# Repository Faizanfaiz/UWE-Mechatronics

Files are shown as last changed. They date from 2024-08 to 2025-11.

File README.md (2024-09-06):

# Single-Leg Robot Dog Project

This repository contains the setup, code, and documentation for the development of a single-leg robot dog. The project is designed to provide a platform for students to experiment with robotic leg control, dynamics, and various motor control algorithms using a Raspberry Pi 5 and RMD X motors.

## Table of Contents
- [Project Overview](#project-overview)
- [Hardware Requirements](#hardware-requirements)
- [Software Setup](#software-setup)
- [License](#license)

## Project Overview
The objective of this project is to develop a single robotic leg that can be used as a testbed for students learning about robotic control systems, motor dynamics, and gait patterns. The robotic leg is powered by RMD X motors and controlled via a Raspberry Pi 5, interfaced through a Waveshare 2-Channel CAN FD HAT. This platform allows for practical experimentation in a controlled environment.

## Hardware Requirements
For the full list of hardware and BOM click [here](https://github.com/Faizanfaiz/UWE-Mechatronics/tree/main/Parts#hardware)
- Raspberry Pi 5
- Waveshare 2-Channel CAN HAT
- RMD-X8 Motors
- Power Supply for Raspberry Pi and Motors
- MicroSD Card (with Raspberry Pi OS 64-bit installed)
- Mechanical components for the robotic leg (joints, frame, etc.)
- CAN Bus cables and connectors

## Software Setup
### 1. Install Raspberry Pi OS (64-bit)
Ensure your Raspberry Pi is running the 64-bit version of Raspberry Pi OS.

### 2. Setup Waveshare 2-CH CAN HAT/ 2-CH CAN FD HAT
Before Following any of the instructions below, make sure you check your expnasion Board and Follow the relevant Instructions:

Follow the instructions provided by Waveshare to set up the 2-Channel CAN HAT. The detailed guide can be found here: [Waveshare 2-CH CAN HAT Setup Guide](https://www.waveshare.com/wiki/2-CH_CAN_HAT).

Follow the instructions provided by Waveshare to set up the 2-Channel CAN FD HAT. The detailed guide can be found here: [Waveshare 2-CH CAN FD HAT Setup Guide](https://www.waveshare.com/wiki/2-CH_CAN_FD_HAT).

### 3. Install Required Dependencies
Install the necessary software packages and dependencies for motor control and CAN communication:
\`\`\`bash
sudo apt-get update
sudo apt-get install can-utils python-can
\`\`\`

### 4. Configure the CAN Interface
Configure the CAN interface to communicate with the RMD X motors. Follow the Waveshare guide for initial setup, and then set the bitrate and interface settings as needed:
\`\`\`bash
sudo ip link set can0 up type can bitrate 1000000
\`\`\`

## License
This project is licensed under a proprietary license for exclusive use by [University Name]. Unauthorized use outside the university is prohibited.

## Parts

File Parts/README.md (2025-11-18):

[pointers to item links below]: #

[RMD-x8]: https://uk.robotshop.com/products/my-actuator-rmd-x8-pro-v2-can-bus-bldc-actuator-w-19-reduction-mc-x-300-o-driver
[PI]: https://thepihut.com/products/raspberry-pi-5?variant=42531604955331
[SD]: https://uk.rs-online.com/web/p/sd-cards/2836581
[CAN-HAT]: https://www.waveshare.com/2-ch-can-fd-hat.htm

[M4I]: https://ebay.us/m/BUPcYn
[M4x30C]: https://ebay.us/m/XLIqXn
[M4x20C]: https://ebay.us/m/y3svrC
[M4x16C]: https://ebay.us/m/ICN1YX
[M4x8C]: https://ebay.us/m/ASdklv
[M4x10CS]: https://ebay.us/m/useJ9E
[M5x35BH]: https://ebay.us/m/N0DYHb
[M5N]: https://ebay.us/m/qY9aDb
[M4N]: https://ebay.us/m/3rJfDg
[TP26]: https://www.bearingboys.co.uk/5M-Section-Timing-Pulley-5mm/265M15-Metric-Pilot-Bore-Timing-Pulley-21236-p
[TB635]: https://www.bearingboys.co.uk/5M-Section-5mm-Pitch/6355M15-Timing-Belt-6109-p
[B22]: https://www.bearingboys.co.uk/Miniature-Bearings/6082RS-Dunlop-Sealed-Miniature-Steel-Ball-Bearing-8mm-x-22mm-x-7mm-7728-p
[B12]: https://www.bearingboys.co.uk/Miniature-Bearings/MR128ZZ-Budget-Shielded-Miniature-Ball-Bearing-8mm-x-12mm-x-35mm--140413-p

[EX2020]: https://ooznest.co.uk/product/20x20mm-t-v-slot-aluminium-extrusion-profile-silver-cut-to-size/
[SBR12]: https://ebay.us/m/hoO5Eb

# Parts list
This document shows everything needed to build the leg, for the assembly please read the [Assembly Guide](https://github.com/Faizanfaiz/UWE-Mechatronics/tree/main/Assembly#assembly). 

## 3D prints
>[!NOTE]
>All parts can fit on a minimum printer bed size of 256x256mm.  
>Everything was printed on the Bambu Lab A1 and X1 Carbon in PolyTerra PLA Fossil Grey.

### Print settings
- 35% infill
- Triangular infill
- Supports enabled
- 2 or 3 layer thick walls
- Bottom Z distance = 0.08mm
- Outer and inner brim 5mm

### 
| Thumbnail | Name | Quantity |
|:---:|:---:|:---:|
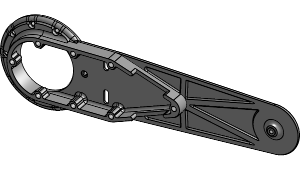
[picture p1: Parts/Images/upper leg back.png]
|  | upper leg back | 1 |
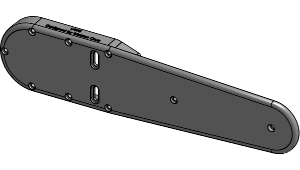
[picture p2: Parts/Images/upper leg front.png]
|   | upper leg front | 1 |
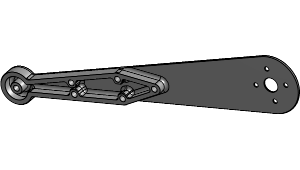
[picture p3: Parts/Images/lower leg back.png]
|  | lower leg back | 1 |
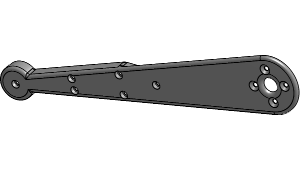
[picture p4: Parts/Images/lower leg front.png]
|   | lower leg front | 1 |
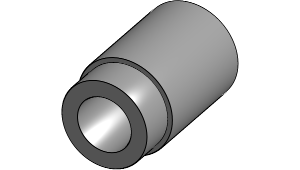
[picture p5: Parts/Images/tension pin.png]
|  | tension pin | 4 |
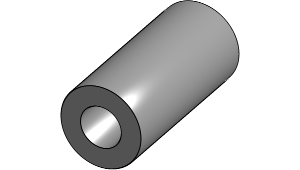
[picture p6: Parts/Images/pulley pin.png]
|  | pulley pin | 1 |
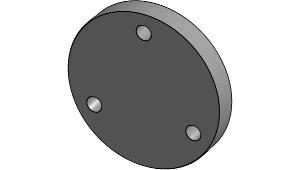
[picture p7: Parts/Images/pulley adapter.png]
|  | pulley adapter | 1 |
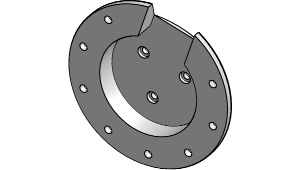
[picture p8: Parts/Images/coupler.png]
|  | coupler | 1 |
|  | motor plate | 1 |

### Depreciated
| Thumbnail | Name | Reason |
|:---:|:---:|:---:|
| | | |

## Hardware
### Electronics needed
>[!NOTE]
>The motor can be swapped for similar motors with same diameter and bolting layout.

| Item + Link | Short description | Quantity | Cost per item |
|---|---|:---:|:---|
| [RMD-X8 motor][RMD-x8] | drive the upper and lower leg | 2 | ~£400 |
| [Raspberry pi 5 8GB][PI] | main board for executing code | 1 | £76.80 |
| [waveshare 2CH CAN FD HAT][CAN-HAT] | SPI to CAN conversion | 1 | £35.75 |
| [SD card 32GB][SD] | raspeberry pi os 64x installed | 1 | £9.98 |
| **Total** | | | **£1,322.53** |

### Hardware for the leg
| Item + Link | Short description | Quantity | Cost per item/pack |
|:---|:---|:---:|:---|
| [M4 inserts][M4I] | one side of both upper and lower leg | 14 | £6.49 / 50 pack |
| [M4x30 cap][M4x30C] | pulley pin | 1 | £3.42 / 5 pack |
| [M4x20 cap][M4x20C] | upper leg enclosure | 8 | £3.84 / 10 pack |
| [M4x16 cap][M4x16C] | lower leg enclosure | 6 | £3.54 / 10 pack |
| [M4x8 cap][M4x8C] | coupler between both motors and the leg | 11 | £4.00 / 20 pack |
| [M4x10 countersunk][M4x10CS] | attaching driven pulley to lower leg | 8 | £3.03 / 10 pack |
| [M5x35 button head][M5x35BH] | pulley tensioner | 2 | £3.54 / 5 pack |
| [M5 nut][M5N] | pulley tensioner | 2 | £2.64 / 5 pack |
| [M4 nut][M4N] | pulley pin | 1 | £2.64 / 5 pack |
| [26-5M-15 Timing Pulley][TP26] | moving the lower leg | 2 | £8.20 |
| [635-5M-15 Timing Belt][TB635] | moving the lower leg | 1 | £7.37 |
| [22x8x7mm bearing][B22] | for the pulleys | 3 | £2.04 |
| [12x8x3.5mm bearing][B12] | for the belt tensioner | 4 | £2.61 |
| **Total** | | | **£67.76** |

### Hardware for the frame
| Item + Link | notes | Quantity | cost per item  |
|:---|:---|:---:|:---|
| [2020 extrusion 1.2m][EX2020] | cut/ordered to length  | 3 | £9.22 |
| [SBR12 linear guide rail 500mm 2pcs][SBR12] | | 2 | £26.59 |
| **Total** | | | **£80.84** |

### Total cost: ~£1,471.13 (Subject to change)

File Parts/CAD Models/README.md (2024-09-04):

This folder contains all the 3D models for the robot leg.

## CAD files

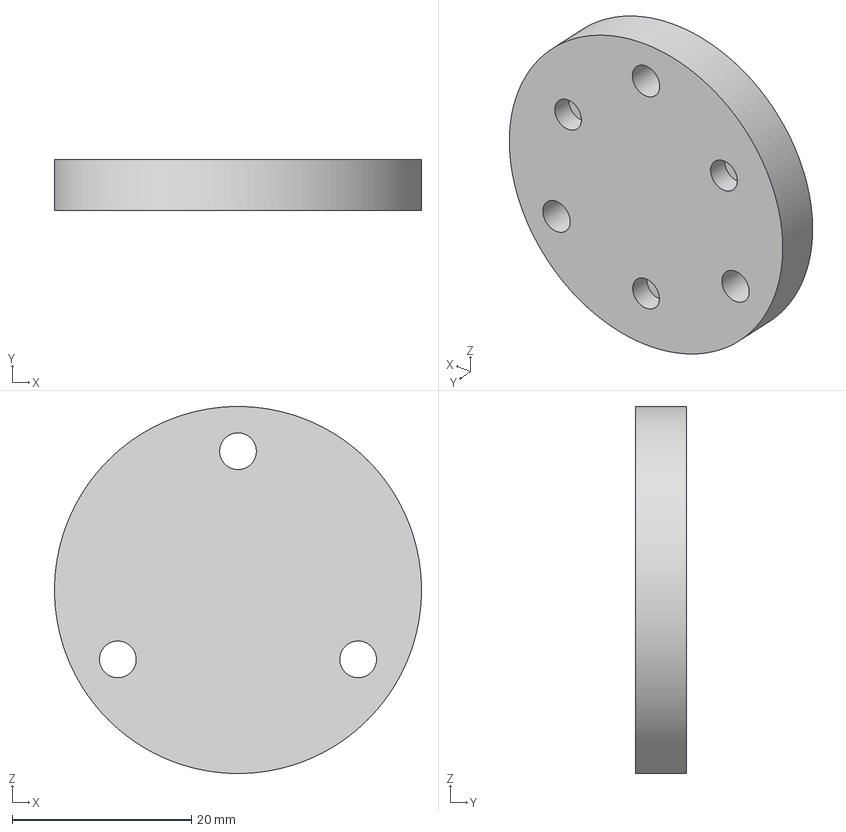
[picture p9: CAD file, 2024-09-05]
Parts/CAD Models/driver pulley adapter.3mf
41.0 x 5.75 x 41.0 mm

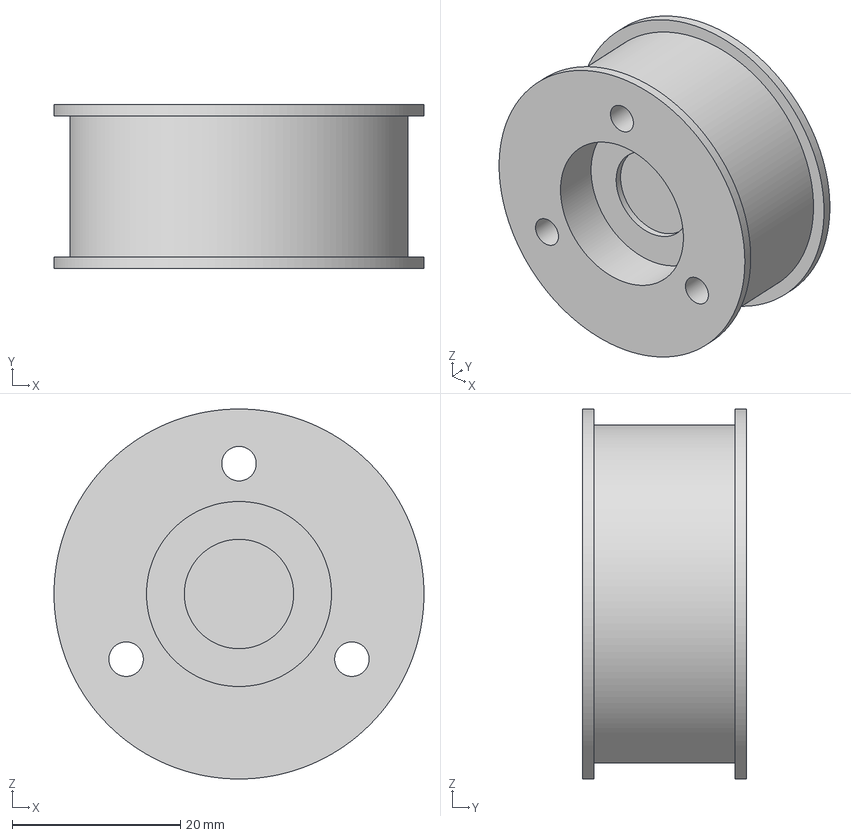
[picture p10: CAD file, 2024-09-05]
Parts/CAD Models/driver pulley.3mf
44.0 x 19.5 x 44.0 mm

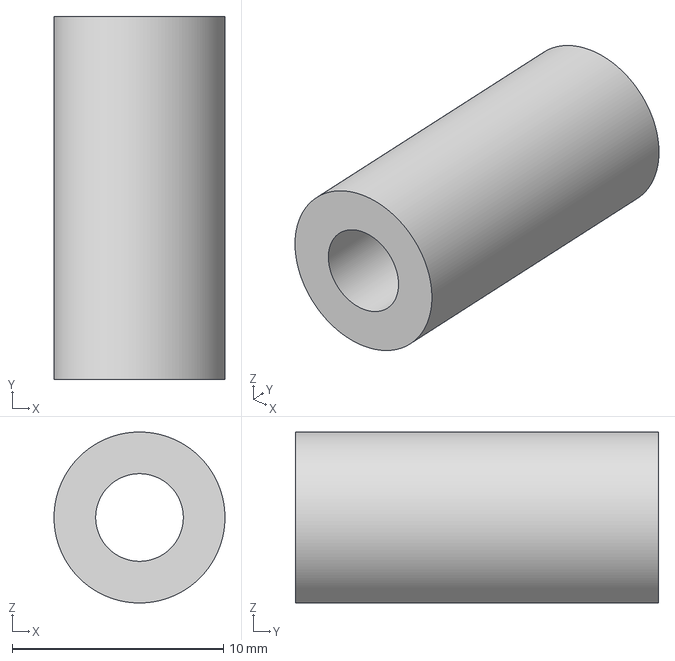
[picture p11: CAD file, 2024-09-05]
Parts/CAD Models/bearing pin.3mf
8.10 x 17.2 x 8.10 mm

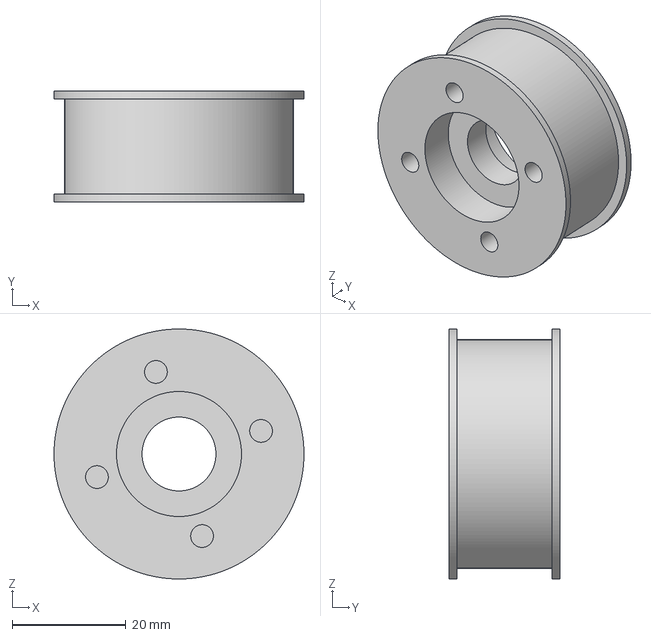
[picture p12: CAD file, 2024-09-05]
Parts/CAD Models/driven pulley.3mf
44.0 x 19.5 x 44.0 mm

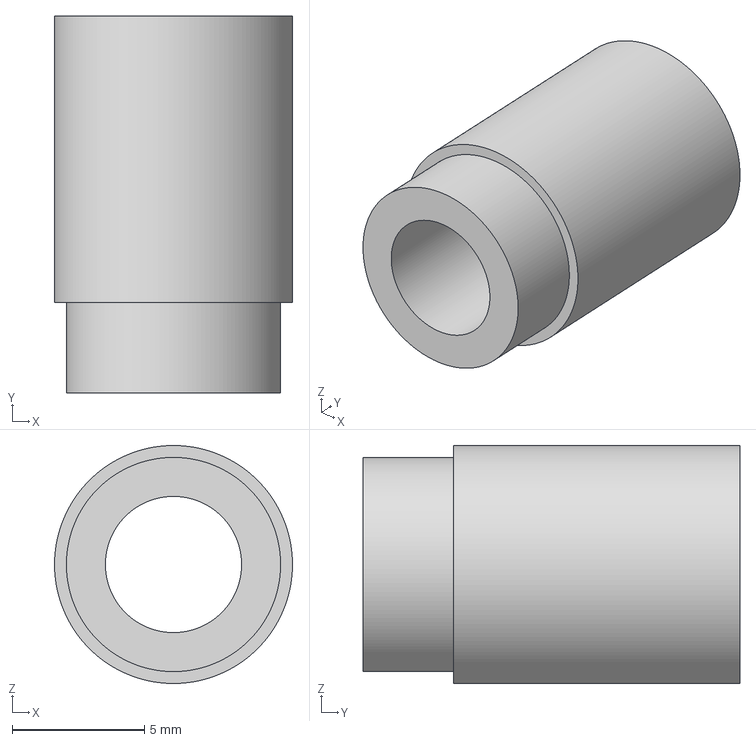
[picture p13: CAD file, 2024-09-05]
Parts/CAD Models/tension pin.3mf
9.00 x 14.2 x 9.00 mm

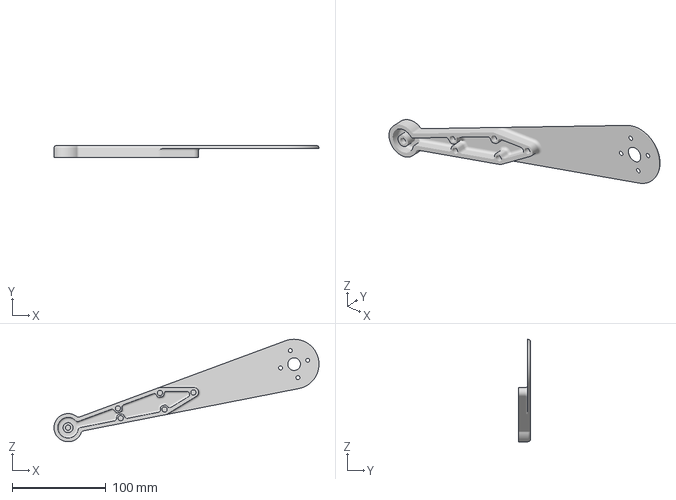
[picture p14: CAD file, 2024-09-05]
Parts/CAD Models/lower leg.3mf
282.2 x 12.8 x 109.1 mm

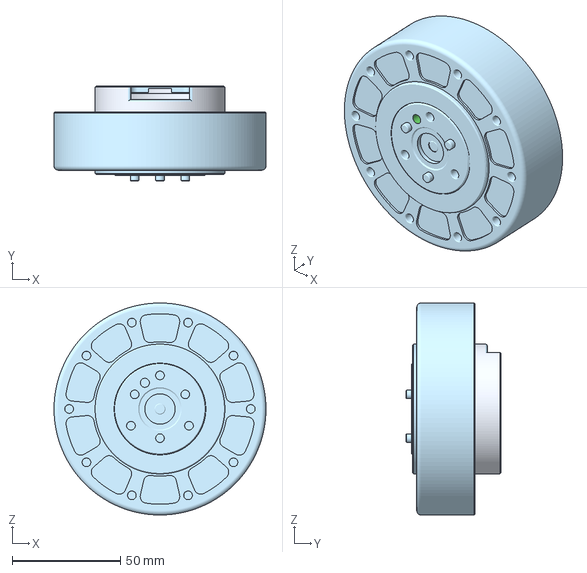
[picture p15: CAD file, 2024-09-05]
Parts/CAD Models/RMD-X8.3mf
98.0 x 44.0 x 98.0 mm

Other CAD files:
Parts/CAD Models/lower leg cover.3mf

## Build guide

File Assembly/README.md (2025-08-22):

# Assembly
This document shows the assembly process for the [robot leg](#robot-leg) and [frame](#frame). Ensure that you have all the [hardware](https://github.com/Faizanfaiz/UWE-Mechatronics/blob/main/Parts/README.md#hardware) and [3D-prints](https://github.com/Faizanfaiz/UWE-Mechatronics/blob/main/Parts/README.md#3d-prints) from the [Parts](https://github.com/Faizanfaiz/UWE-Mechatronics/tree/main/Parts#parts-list) list.

>[!NOTE]
>Previously assembled components may be excluded from some images to simplify the viewing of each step. Compare your build to the checks along the way.

# Robot leg
>[!IMPORTANT]
>Before starting the leg assembly, heat press the M4 threaded inserts into the holes labeled below. [Here](https://youtu.be/P7nHyI1TwKY?t=188&si=k5AsJouK1HimsCW4) is a video explaining how to do this.

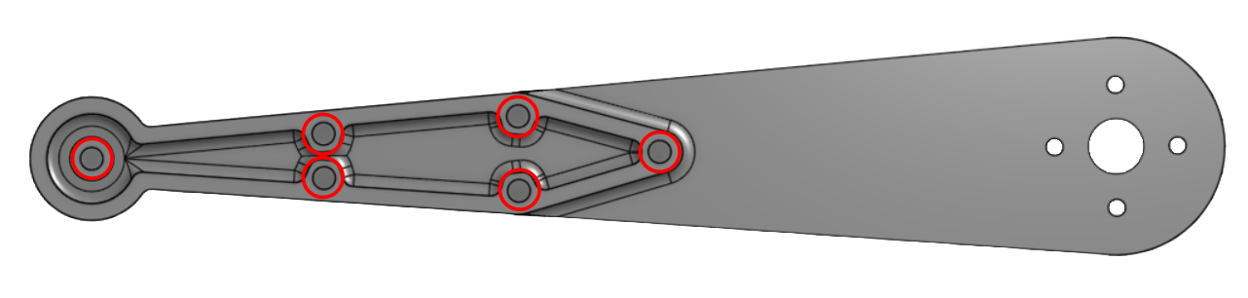
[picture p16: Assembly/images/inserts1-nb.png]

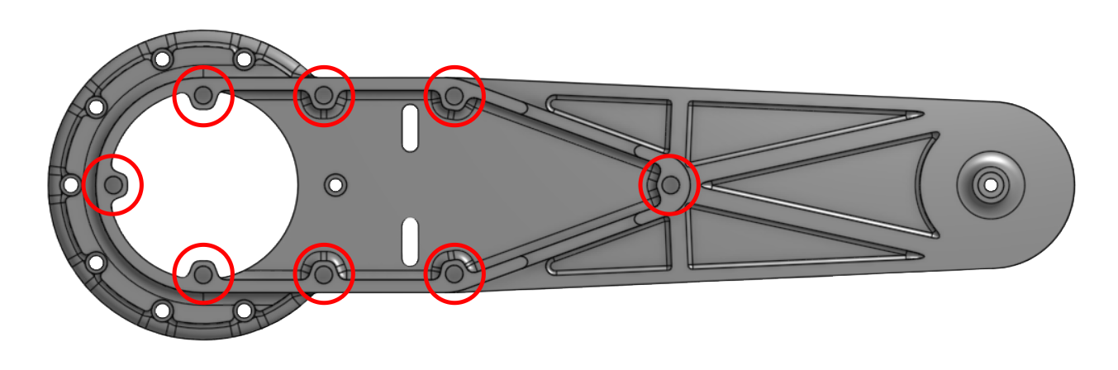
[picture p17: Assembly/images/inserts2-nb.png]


>[!IMPORTANT]
>Press the bearings into the driver and driven pulleys before assembly.

## Lower leg

### Step 1
Press fit the **22 × 8 × 7 mm bearings** into the lower leg driven pulley.  
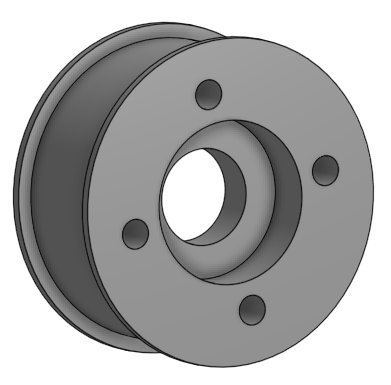
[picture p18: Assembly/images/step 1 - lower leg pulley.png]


### Step 2
Use 6 **M4 × 16 mm cap bolts** to connect the front and back plates of the lower leg. Place the belt between the two plates, then insert the driven pulley. Align the screw holes with the leg (on the right) and secure the pulley using 8 **M4 × 10 mm countersunk bolts**, 4 on each side.  
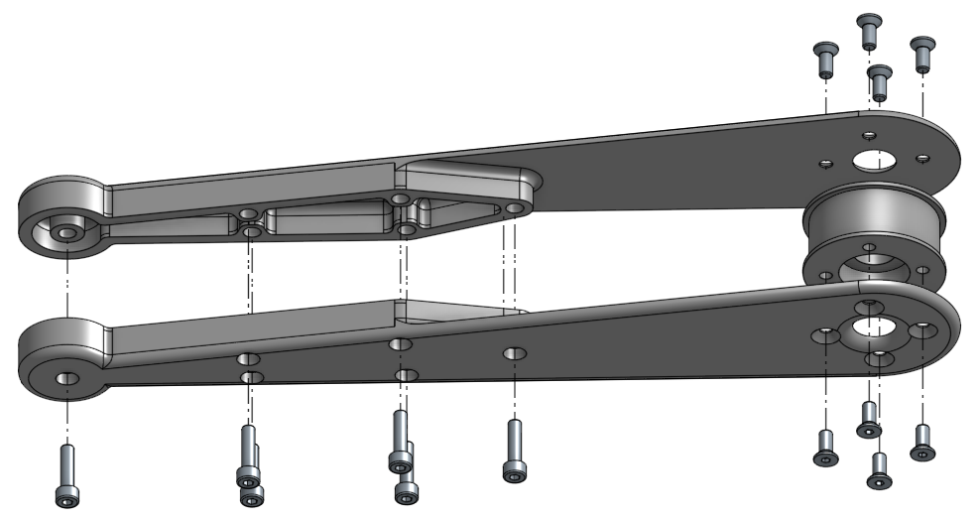
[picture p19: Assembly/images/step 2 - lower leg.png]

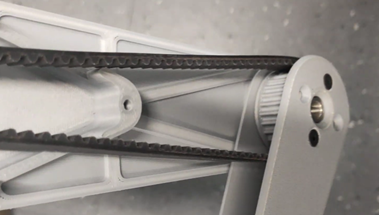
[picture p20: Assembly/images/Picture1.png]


### Check
The lower leg should now look like this:  
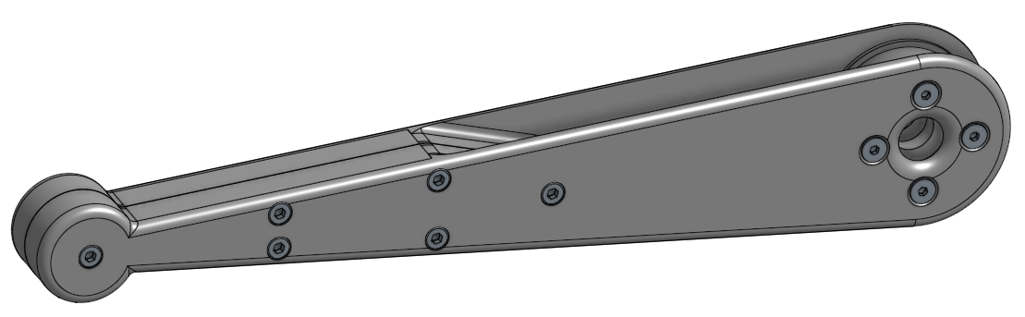
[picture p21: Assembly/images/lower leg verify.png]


## Upper leg

### Step 1
Use 3 **M4 × 8 mm cap bolts** to connect the coupler to the upper leg motor. Ensure that the pins on the motor hub are seated properly.  
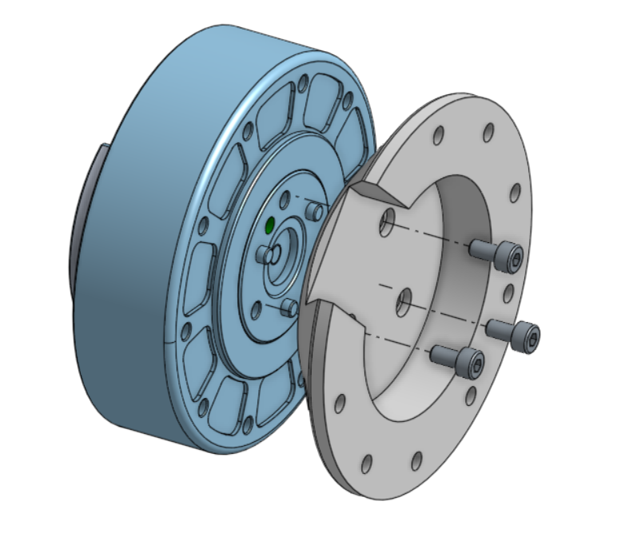
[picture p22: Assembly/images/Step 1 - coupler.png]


### Step 2
>[!NOTE]
>These bolts are slightly harder to screw in because there is limited clearance around the upper leg motor. Use an Allen key with a short side, or cut one down if needed.

Use 8 **M4 × 8 mm cap bolts** to secure the lower leg motor to the coupler.  
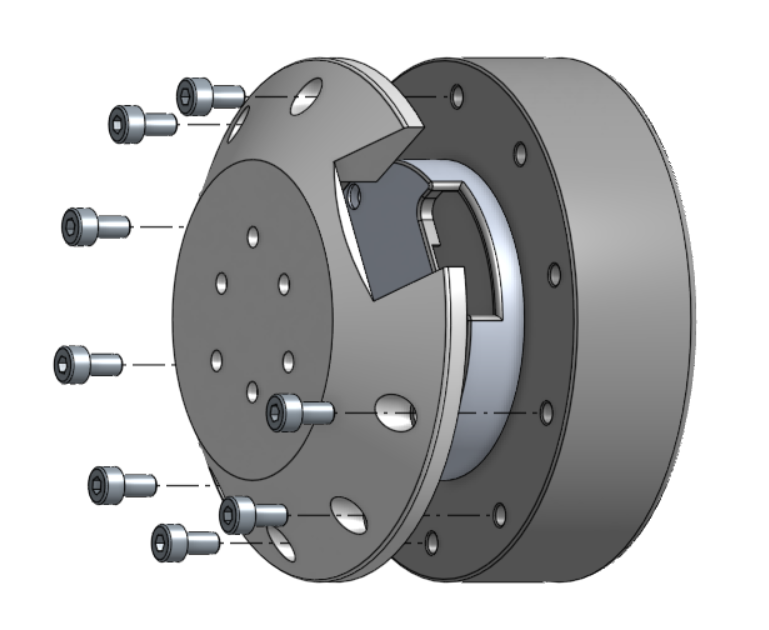
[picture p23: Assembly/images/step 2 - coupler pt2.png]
  

### Check
The assembly should now look like this:  
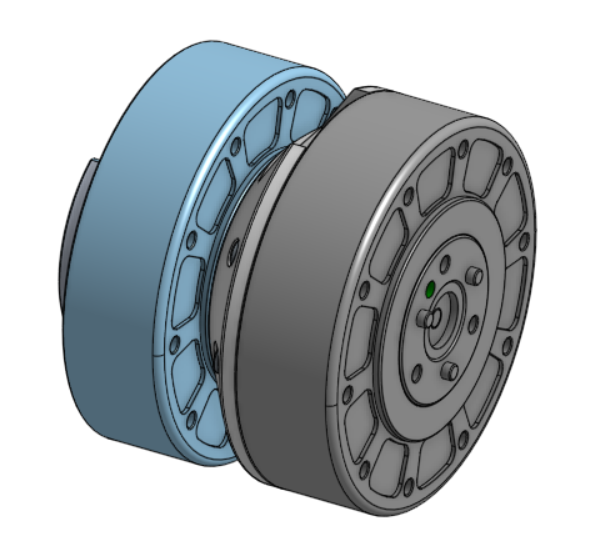
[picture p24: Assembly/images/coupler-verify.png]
  

### Step 3
Use 7 **M4 × 8 mm cap bolts** to mount the upper leg back plate to the lower leg motor.  
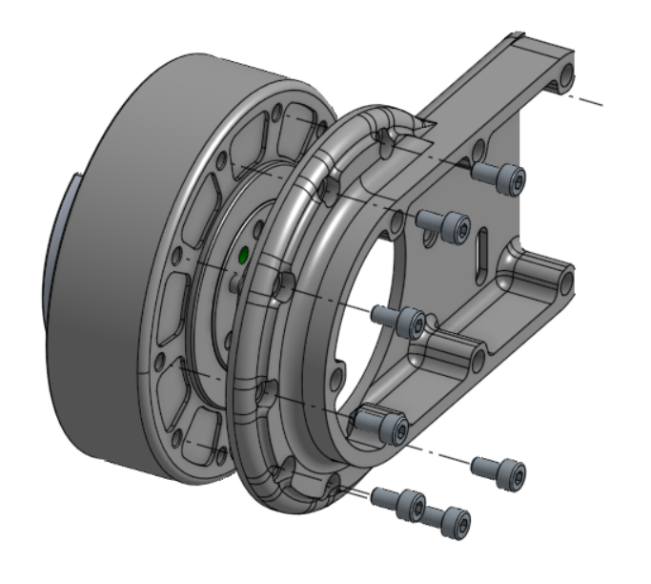
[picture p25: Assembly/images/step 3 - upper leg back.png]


### Step 4
Place the driver pulley and adapter onto the lower leg motor and secure them using 3 **M4 × 30 mm pan head bolts**.  
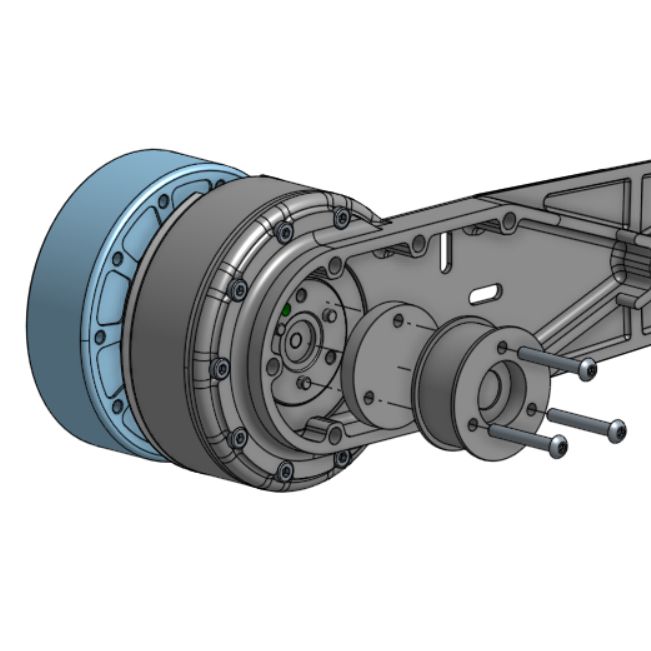
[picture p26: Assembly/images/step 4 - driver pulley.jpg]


### Step 5
Press fit four **12 × 8 × 3.5 mm bearings** into each tension pin.  
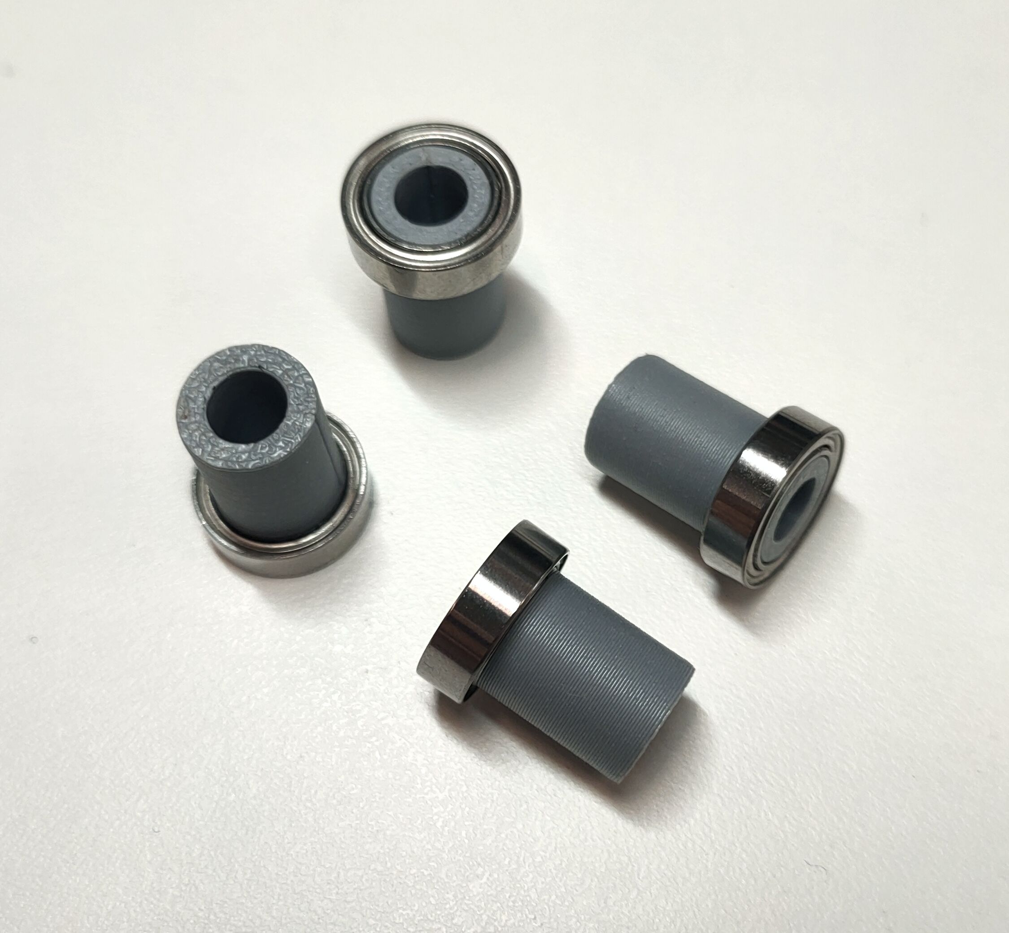
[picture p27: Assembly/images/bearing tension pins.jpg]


### Step 6
Align the tension pins, pulley pin, and lower leg with the upper leg back plate as shown.  
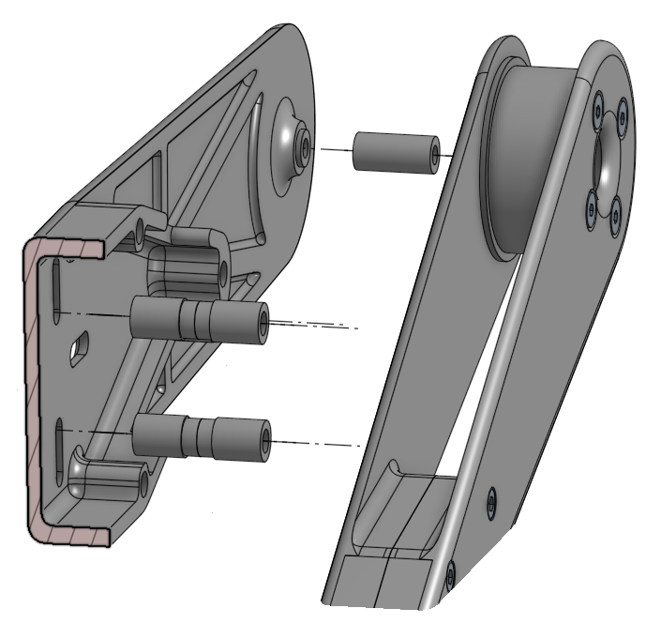
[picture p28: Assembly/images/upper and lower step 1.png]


Place the belt around the driver pulley so it looks like this:

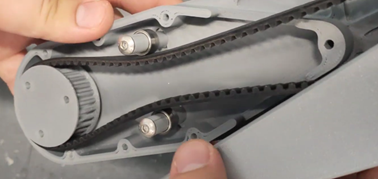
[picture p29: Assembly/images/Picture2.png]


### Step 7
Place the upper leg front plate onto the assembly. Secure both halves together using 8 **M4 × 20 mm cap bolts**. Insert 2 **M5 × 35 mm pan head bolts** through the tension pins, and 1 **M4 × 30 mm cap bolt** through the pulley pin.  
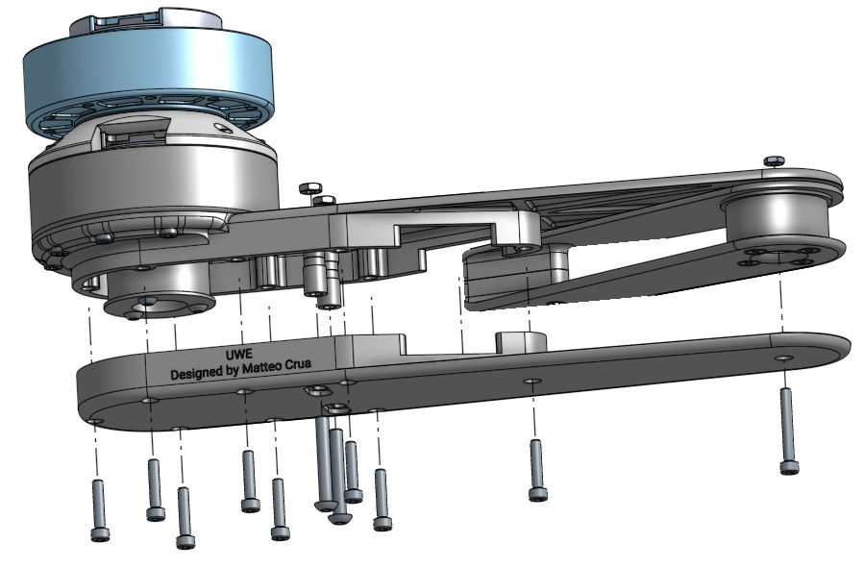
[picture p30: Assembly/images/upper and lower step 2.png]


## Check
The completed robot leg should look like this:  

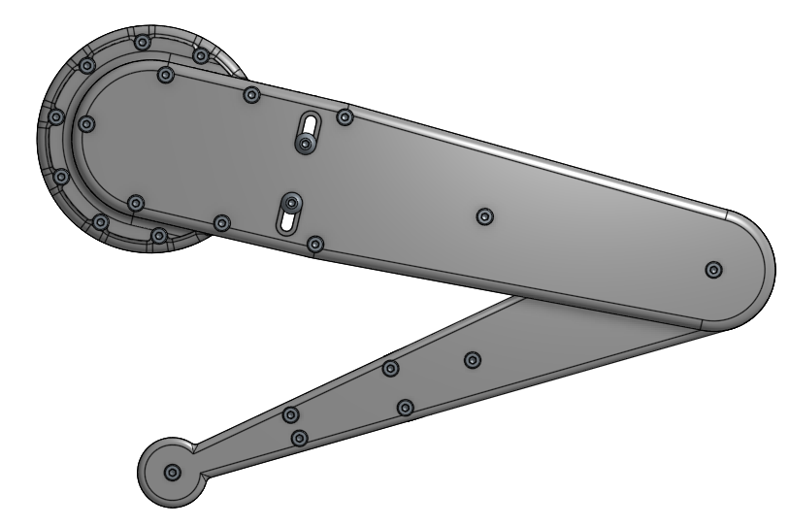
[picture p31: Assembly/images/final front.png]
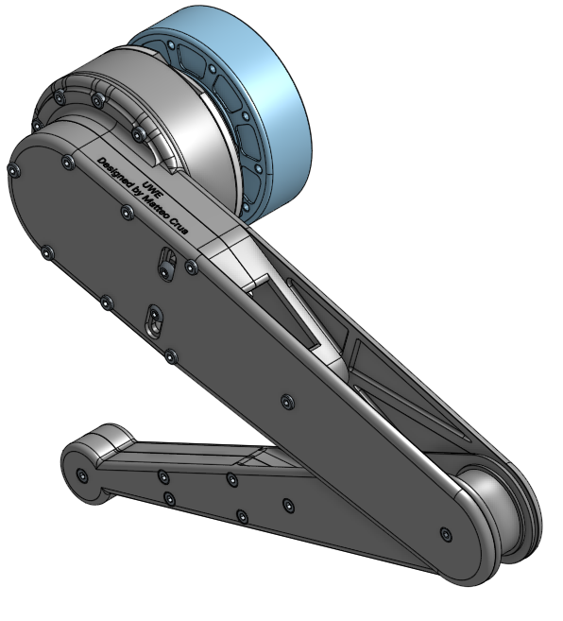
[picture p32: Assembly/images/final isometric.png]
 

# Wiring schematic
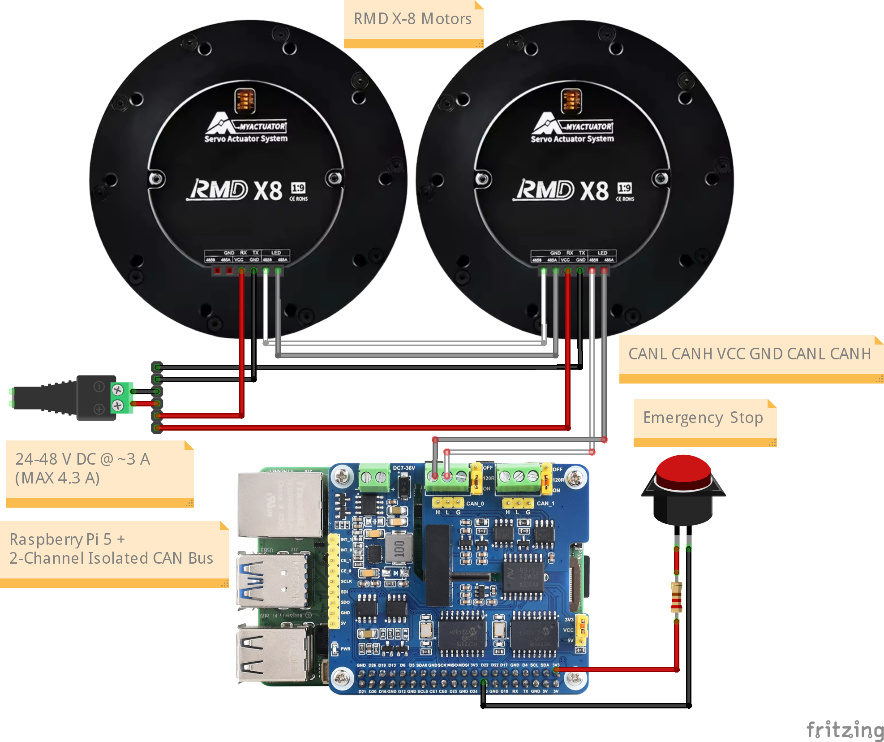
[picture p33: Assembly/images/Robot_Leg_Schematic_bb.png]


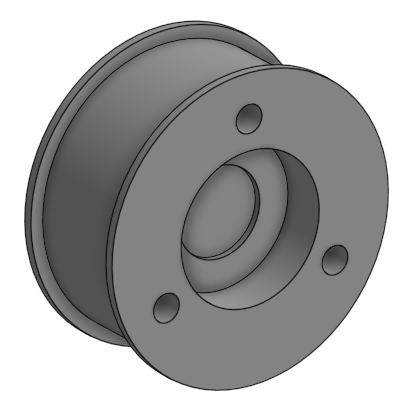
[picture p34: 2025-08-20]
Assembly/images/step 5 driver pulley.png

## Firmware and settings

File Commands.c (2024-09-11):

/*****************************************************************************
 *                                                                           *
 *                     ██╗   ██╗██╗    ██╗███████╗                           *
 *                     ██║   ██║██║    ██║██╔════╝                           *
 *                     ██║   ██║██║ █╗ ██║█████╗                             *
 *                     ██║   ██║██║███╗██║██╔══╝                             *
 *                     ╚██████╔╝╚███╔███╔╝███████╗                           *
 *                      ╚═════╝  ╚══╝╚══╝ ╚══════╝                           *
 *                                                                           *
 *   Kinematics for Robot Leg Engineered by FAIZAN MIR                       *
 *   Date: September 2024                                                    *
 *   For the UWE RMD X8 Motors     											 *
 * 																			 *
 *	 MCP2515 controller with SPI interface was used                          *
 *                                                                           *
 *   The Work was conducted for the UWE Engineering Mechatronics LAB         *
 *                                                                           *
 *   Project Partner: Matteo Ciua                                            *
 *   Project Supervisor: Appolinaire Etoundi                                 *
 *   Project Technician: Romain Derval                                       *
 *                                                                           *
 *                                                                           *
 *  To operate the Leg, input commands:                                      *
 *      - Send 0 for Sitting (x = 0, y = -10)                                *
 *      - Send 1 for Standing (x = 10, y = -70)                              *
 *      - Send 2 for Hopping (requires standing first)                       *
 *****************************************************************************/

#include <stdio.h>
#include <math.h>
#include <stdint.h>
#include <unistd.h>
#include <signal.h>
#include <stdbool.h>

#define PI 3.14159265358979323846
#define L1 55.00
#define L2 55.00

/// Motor library (ensure this header is available in your project)
#define UWERMDX_IMPLEMENTATION
#include "uwermdx.h"

bool is_standing = false; // Track if the dog is in standing position

// Function to calculate angles theta1 and theta2
void inversekinematics(double x, double y, double *theta1_deg, double *theta2_deg) {
    double d = sqrt(x * x + y * y);
    
    // Check if target is within reach
    if (d > (L1 + L2)) {
        printf("Target (%.2f, %.2f) is out of reach. Maximum reach is %.2f.\n", x, y, L1 + L2);
        return;
    }
    
    double cos_theta2 = (d * d - L1 * L1 - L2 * L2) / (2 * L1 * L2);
    double theta2 = acos(cos_theta2);  // Theta 2 in radians
    
    // Ensure correct quadrant for theta2
    if (y < 0) {
        theta2 = -theta2;
    }
    
    // Use atan2 to get correct angle for theta1 in all quadrants
    double theta1 = atan2(y, x) - atan2(L2 * sin(theta2), L1 + L2 * cos(theta2));
    
    // Convert radians to degrees
    *theta1_deg = theta1 * (180.0 / PI);
    *theta2_deg = 180 + theta2 * (180.0 / PI);
}

// Function to check if the point is in the 3rd or 4th quadrant
int is_valid_quadrant(double x, double y) {
    if ((x <= 0 && y <= -10) || (x >= 0 && y <= -10) || (x >= 0 && y >= -90) || (x <= 0 && y >= -90)) {
        return 1;  // Valid coordinate
    }
    printf("Coordinates (%.2f, %.2f) are in the 1st or 2nd quadrant, which are not allowed.\n", x, y);
    return 0;  // Invalid coordinate
}

// Function to send command-based positions
void execute_command(int command) {
    double x = 0, y = 0;
    double joint1, joint2;
    
    switch (command) {
        case 0:
            // Sitting position
            x = 0;
            y = -10;
            is_standing = false; // Update the state to indicate the dog is sitting
            break;
        case 1:
            // Standing position
            x = 10;
            y = -70;
            is_standing = true;  // Update the state to indicate the dog is standing
            break;
        case 2:
            // Hopping, only allowed if the dog is standing
            if (!is_standing) {
                printf("Dog must be standing before hopping.\n");
                return;
            }
            for (int i = 0; i < 35; ++i) { // Hop 5 times
                x = 10;
                y = (i % 2 == 0) ? -70 : -75;
                inversekinematics(x, y, &joint1, &joint2);
                printf("Hop to position: x=%.2f, y=%.2f\n", x, y);
                send_pos_speed(0x143, joint1, 100);  // Send theta1 to motor 1
                send_pos_speed(0x146, joint2, 100);  // Send theta2 to motor 2
                usleep(100000); // 0.5-second delay between hops
            }
            return;
        default:
            printf("Invalid command\n");
            return;
    }

    // Check if the coordinates are in a valid quadrant
    if (!is_valid_quadrant(x, y)) {
        return;  // If not valid, skip
    }

    // Calculate inverse kinematics
    inversekinematics(x, y, &joint1, &joint2);

    // Send the calculated angles to the motors
    send_pos_speed(0x143, joint1, 20);  // Send theta1 to motor 1
    send_pos_speed(0x146, joint2, 20);  // Send theta2 to motor 2
}

// Signal handler to ensure the dog sits before termination
void handle_termination(int signum) {
    printf("\nTerminating program. Dog will now sit...\n");
    execute_command(0);  // Set the dog to sit
    close_can("can0");    // Close CAN communication
    printf("CAN communication closed. Exiting program.\n");
    exit(0);
}

int main() {
    int command;

    // Motor Control
    uint32_t motors_can0[] = {0x143, 0x146};
    bind_motors("can0", motors_can0, 2); // Bind 2 motors to CAN0

    // Initialize CAN
    init_can("can0", 1000000);

    // Register signal handler to sit the dog on termination
    signal(SIGINT, handle_termination);  // Handle Ctrl+C (SIGINT)

    while (1) {
        // Input command from user
        printf("\nEnter command (0 = Sit, 1 = Stand, 2 = Hop): ");
        scanf("%d", &command);

        // Execute the corresponding command
        execute_command(command);
    }

    return 0;
}

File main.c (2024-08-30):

#define UWERMDX_IMPLEMENTATION
#include "uwermdx.h"
#include <stdint.h>
#include <stdio.h>

int main() {

    uint32_t motors_can0[] = {0x146, 0x142, 0x143, 0x144};
    
    bind_motors("can0", motors_can0, 4); // Bind 4 motors to CAN0

    init_can("can0", 1000000);

    send_pos_speed(0x146, 30, 50); 
    sleep(1);
    send_pos_speed(0x146, 20, 50); 
    sleep(1);
    send_pos_speed(0x146, 30, 50); 
    sleep(1);
    send_pos_speed(0x146, 20, 50); 

        // Example: Read PID parameters from motor with ID 0x141
    PIDParams params;
    if (read_motor_pid_parameters(0x141, &params) == 0) {
        // Print out the PID parameters
        printf("Current loop KP: %.6f\n", params.curr_kp);
        printf("Current loop KI: %.6f\n", params.curr_ki);
        printf("Speed loop KP: %.6f\n", params.spd_kp);
        printf("Speed loop KI: %.6f\n", params.spd_ki);
        printf("Position loop KP: %.6f\n", params.pos_kp);
        printf("Position loop KI: %.6f\n", params.pos_ki);
    } else {
        printf("Failed to read PID parameters from motor 0x141\n");
    }

    // When done, close the CAN interface
    close_can("can0");
    
    close_can("can0");
    
    return 0;
}

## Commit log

2024-09-04 Create README.md for assembly
2024-09-04 Update README.md for assembly
    testing jump to hyperlinks
2024-09-04 added hyperlink to assembly guide
2024-09-04 Create README.md in CAD models
2024-09-04 whole leg CAD files
    [RMD X8.step, bearing pin.step, driven pulley.step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]
2024-09-04 Added BOM to README
    need to find the price of each item and add it
2024-09-04 added motor type
2024-09-04 added all hardware used on the leg
    still need to add price per item
2024-09-04 motor coupler added
    [motor coupler.step]
2024-09-04 separated hardware for leg and frame
2024-09-04 linked the hardware list and BOM to hardware req
2024-09-05 add thumbnail for upper back leg
2024-09-05 removed STEP files for 3mf
    [RMD-X8.3mf, bearing pin.3mf, driven pulley.3mf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]
2024-09-05 added links to hardware and 3d prints
2024-09-05 added print settings and min bed size
2024-09-06 used html format and added coupler
2024-09-06 motor-plate.png added
2024-09-06 coupler verify
2024-09-07 added motor plate
2024-09-11 added inserts instructions
2025-08-20 Update assembly README.md
2025-08-22 Refine assembly instructions for clarity
2025-08-22 Add image for belt placement in assembly instructions
2025-08-22 schematic image
2025-08-22 wiring schematic
2025-08-22 Update README with wiring schematic section
2025-08-22 uploaded editable version of robot leg
    perma-link to Onshape document so that anyone can view and export into different formats:
    https://cad.onshape.com/documents/4c2e64c2cc8ef0c058c6e8d9/w/9789c50df96fff6b564381e6/e/bd21839dc53dd80332bf32b2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
